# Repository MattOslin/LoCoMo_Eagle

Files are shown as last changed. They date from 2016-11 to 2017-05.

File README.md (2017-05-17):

# LoCoMo

Eagle files for LoCoMo boards.

Motherboard is the breakout for ESP-12, including wiperboard, espboard, and usb board. The individual boards are the cut up sections. Note that the motherboard file is for reference only, and the individual boards are the only working copy.

Slipring is the slip ring/potentiometer.

Zigzag is an excellent sheet used to define the start and end points of the traces for the encoder. Look at the zigzag script to see how to format the output of the excel sheet for use in eagle.

DXF files for stencils can be created using the cream-dxf ulp.

The zip files are OSHPARK cam files.

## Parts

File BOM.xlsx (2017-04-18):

Item | Module Quantity | Unit Price | Unit Price @10 | Total | Digikey # | URL | NOTES
4 Position Wiper | 1 | 1.26 | 1.145 | 1.145 | 70AAJ-4-M0-ND | https://www.digikey.com/product-detail/en/bourns-inc/70AAJ-4-M0/70AAJ-4-M0-ND/1232565
Op amp | 1 | 0.43 | 0.349 | 0.349 | AZV321KSTR-G1DICT-ND | http://www.digikey.com/scripts/DkSearch/dksus.dll?Detail&itemSeq=224809805&uq=636271628868311434
2 Position contact | 2 | 0.86 | 0.759 | 1.518 | 70AAJ-2-M0-ND | https://www.digikey.com/product-detail/en/bourns-inc/70AAJ-2-M0/70AAJ-2-M0-ND/1232563
Motor driver | 1 | 1.33 | 1.181 | 1.181 | TB6593FNGCT-ND | http://www.digikey.com/scripts/DkSearch/dksus.dll?Detail&itemSeq=224809802&uq=636271628868311434
Inductor | 1 | 0.21 | 0.192 | 0.192 | 490-10563-1-ND | http://www.digikey.com/scripts/DkSearch/dksus.dll?Detail&itemSeq=224809801&uq=636271628868311434
Vertical mini usb | 1 | 1.04 | 0.918 | 0.918 | H125262-ND | https://www.digikey.com/product-detail/en/hirose-electric-co-ltd/ZX80-B-5P(30)/H125262-ND/5994728
Regulator | 1 | 1.59 | 1.425 | 1.425 | 296-41856-1-ND | http://www.digikey.com/scripts/DkSearch/dksus.dll?Detail&itemSeq=224809799&uq=636271628868311434
Switch | 1 | 0.25 | 0.232 | 0.232 | RN1906FELF(CTCT-ND | http://www.digikey.com/scripts/DkSearch/dksus.dll?Detail&itemSeq=224809798&uq=636271628868311434
Power diode | 1 | 0.36 | 0.291 | 0.291 | B130-FDICT-ND | http://www.digikey.com/scripts/DkSearch/dksus.dll?Detail&itemSeq=224809794&uq=636271634297267434
Bi-LED | 1 | 0.44 | 0.311 | 0.311 | 160-2026-1-ND | http://www.digikey.com/product-detail/en/lite-on-inc/LTST-C235KGKRKT/160-2026-1-ND/3711391
CCR | 1 | 0.44 | 0.374 | 0.374 | NSI45020AT1GOSCT-ND | https://www.digikey.com/product-detail/en/on-semiconductor/NSI45020AT1G/NSI45020AT1GOSCT-ND/2096225
Button | 1 | 0.28 | 0.268 | 0.268 | CKN10502CT-ND | https://www.digikey.com/product-detail/en/c-k/PTS810-SJM-250-SMTR-LFS/CKN10502CT-ND/4176673
Clock | 1 | 1.11 | 0.984 | 0.984 | 631-1116-1-ND | http://www.digikey.com/scripts/DkSearch/dksus.dll?Detail&itemSeq=224809792&uq=636271634297267434
Header pins | 1 | 0.56 | 0.389 | 0.389 | S9014E-04-ND | https://www.digikey.com/product-detail/en/sullins-connector-solutions/GRPB041VWVN-RC/S9014E-04-ND/1786440
CH340G | 1 | 0.5 | 0.25 | 0.25 |  | EBAY
ESP12 | 1 | 2 | 1 | 1
1K Resistor | 2 |  |  |  |  |  | STOCK
5.1K Resistor | 1
330Ohm Resistor | 2
10K Resistor | 5 |  |  |  |  |  | STOCK
470Ohm Resistor | 2
100nF Capacitor | 5
10uF Capacitor | 3
2.2uF Capacitor | 1 |  |  |  |  |  | STOCK
22uF Capacitor | 1 |  |  |  |  |  | STOCK
10pF Capacitor | 1 |  |  |  |  |  | STOCK
15pF Capacitor | 1
 |  |  |  | 10.827

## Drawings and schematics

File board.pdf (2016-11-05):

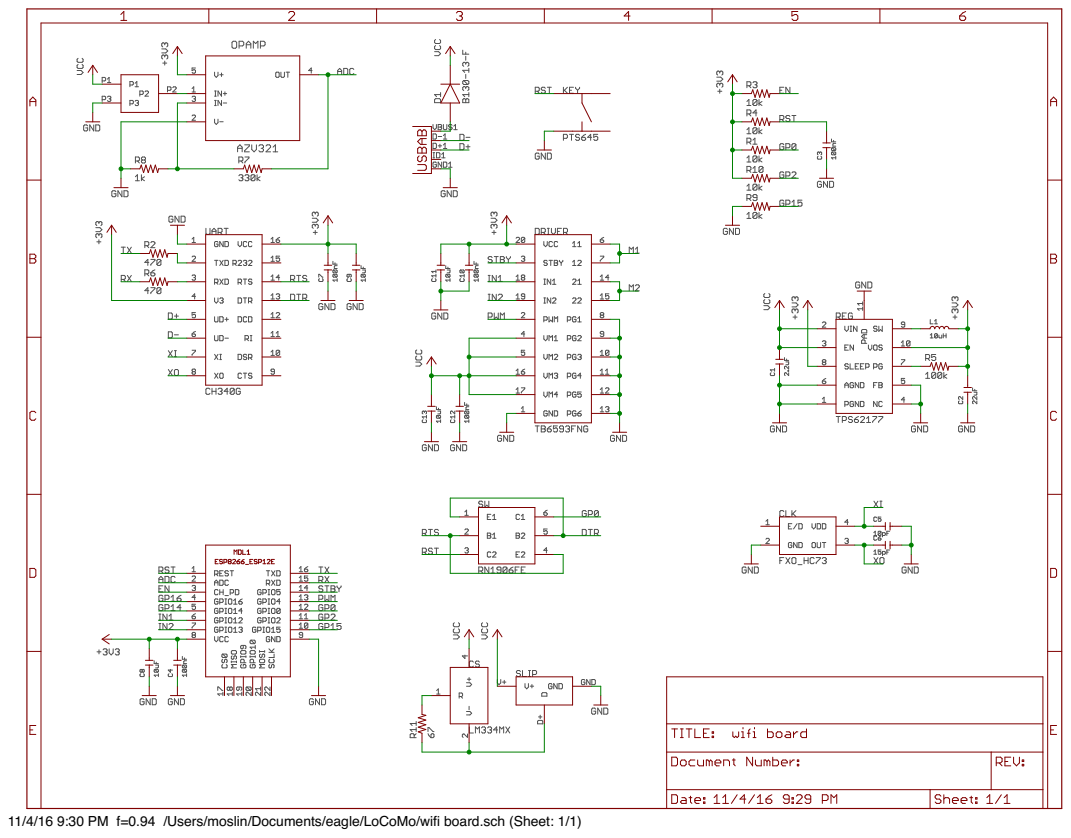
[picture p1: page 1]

11/4/16 9:30 PM f=0.94 /Users/moslin/Documents/eagle/LoCoMo/wifi board.sch (Sheet: 1/1)

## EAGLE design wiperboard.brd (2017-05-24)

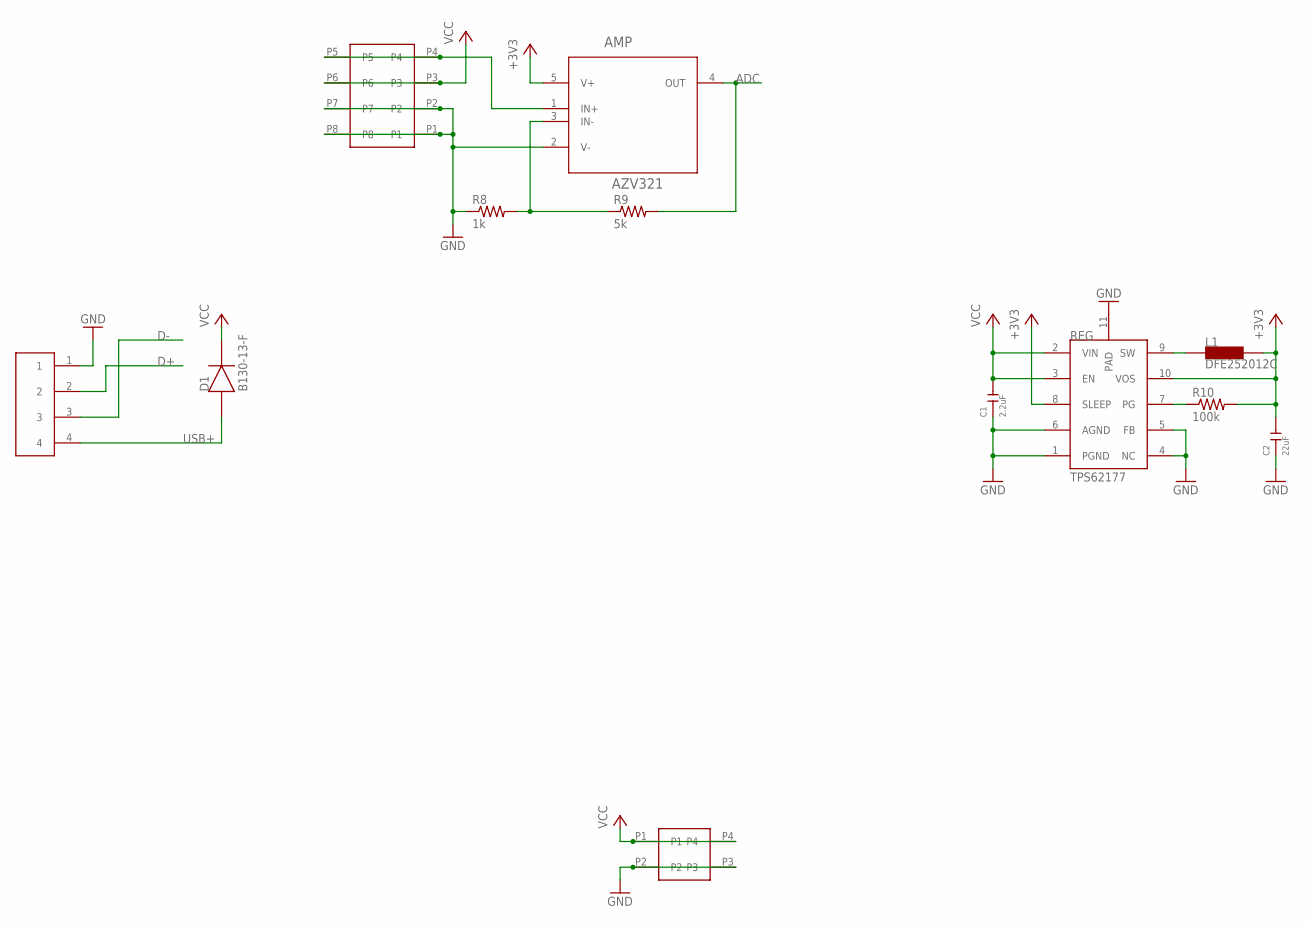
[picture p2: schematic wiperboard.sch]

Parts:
AMP: AZV321; SOT65P210X110-5N
C1: 2.2uF; C0603
C2: 22uF; C0603
CONN: BOURNS_2PIN
D1: B130-13-F; SMA
L1: DFE252012C; 1008
R8: 1k; R0603
R9: 5k; R0603
R10: 100k; R0603
REG: TPS62177; WSON-10
U$3: 4PIN_HEADER
WIPER: BOURNS_4PIN

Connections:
+3V3: AMP.5 (V+), C2.2, L1.P$3, R10.2, REG.8 (SLEEP), REG.10 (VOS)
ADC: AMP.4 (OUT), R9.2
D+: U$3.2
D-: U$3.3
GND: AMP.2 (V-), C1.1, C2.1, CONN.P2, CONN.P3, R8.1, REG.1 (PGND), REG.4 (NC), REG.5 (FB), REG.6 (AGND), REG.11 (PAD), U$3.1, WIPER.P1, WIPER.P2, WIPER.P7, WIPER.P8
unnamed: R10.1, REG.7 (PG)
unnamed: AMP.1 (IN+), WIPER.P4, WIPER.P5
unnamed: AMP.3 (IN-), R8.2, R9.1
SW: L1.P$2, REG.9 (SW)
USB+: D1.AN, U$3.4
VCC: C1.2, CONN.P1, CONN.P4, D1.CATH, REG.2 (VIN), REG.3 (EN), WIPER.P3, WIPER.P6

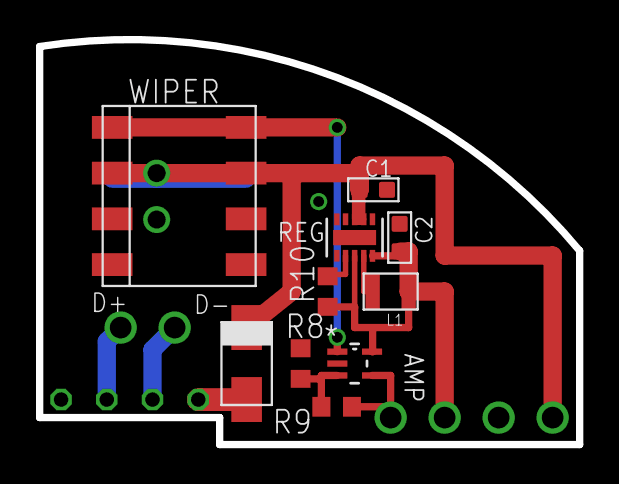
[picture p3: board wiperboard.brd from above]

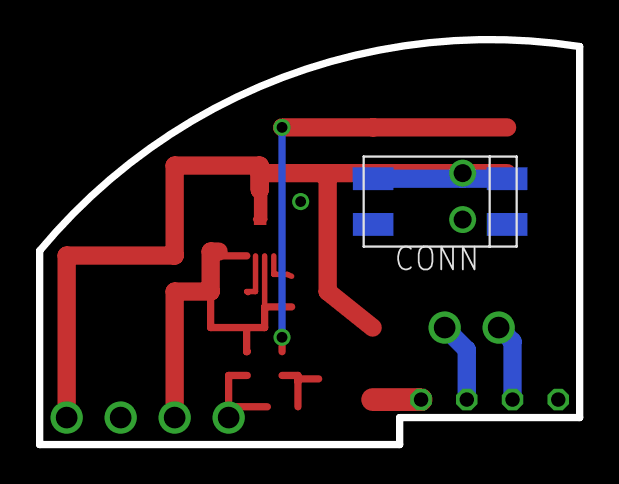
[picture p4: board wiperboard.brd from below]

Board: 2 copper layers, 30.0 x 22.5 mm, 12 parts (2 on the bottom side), 9 nets.

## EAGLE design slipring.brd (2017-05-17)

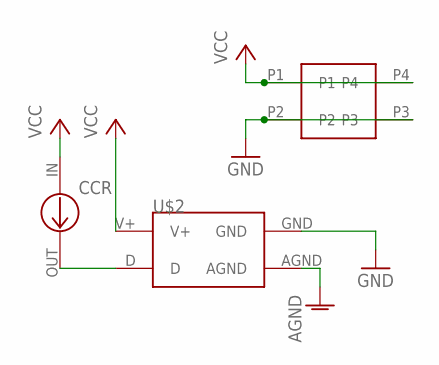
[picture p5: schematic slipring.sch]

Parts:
CCR: CCR
CONN: BOURNS_2PIN
U$2: RING3

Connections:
AGND: U$2.AGND
GND: CONN.P2, CONN.P3, U$2.GND
unnamed: CCR.OUT, U$2.D
VCC: CCR.IN, CONN.P1, CONN.P4, U$2.V+

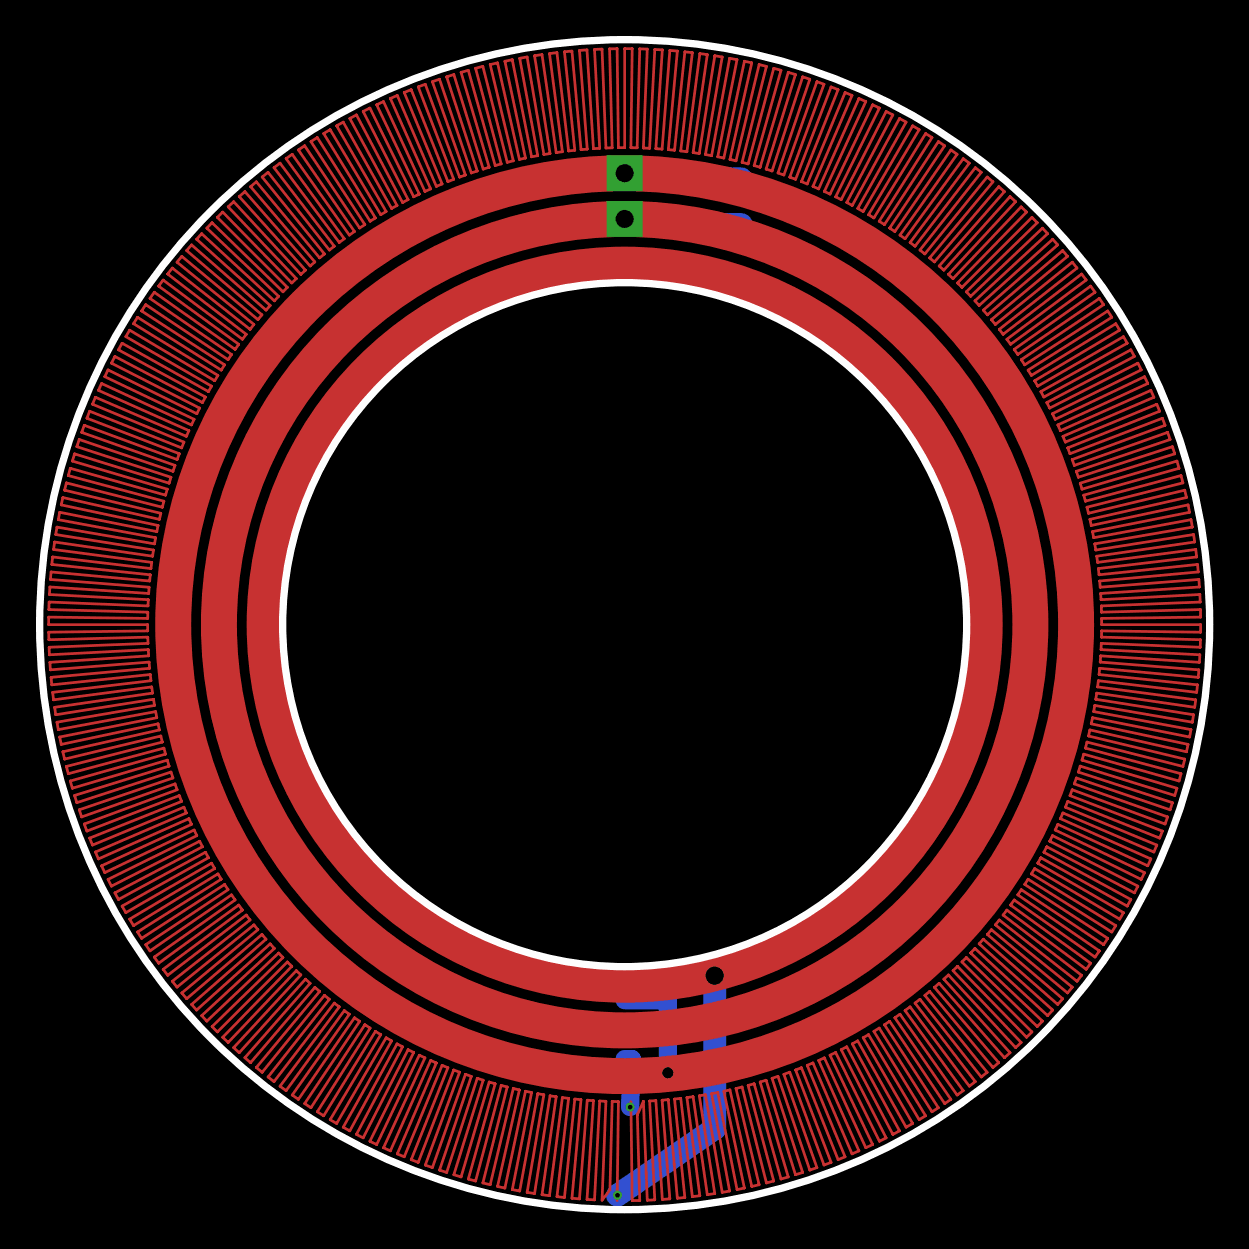
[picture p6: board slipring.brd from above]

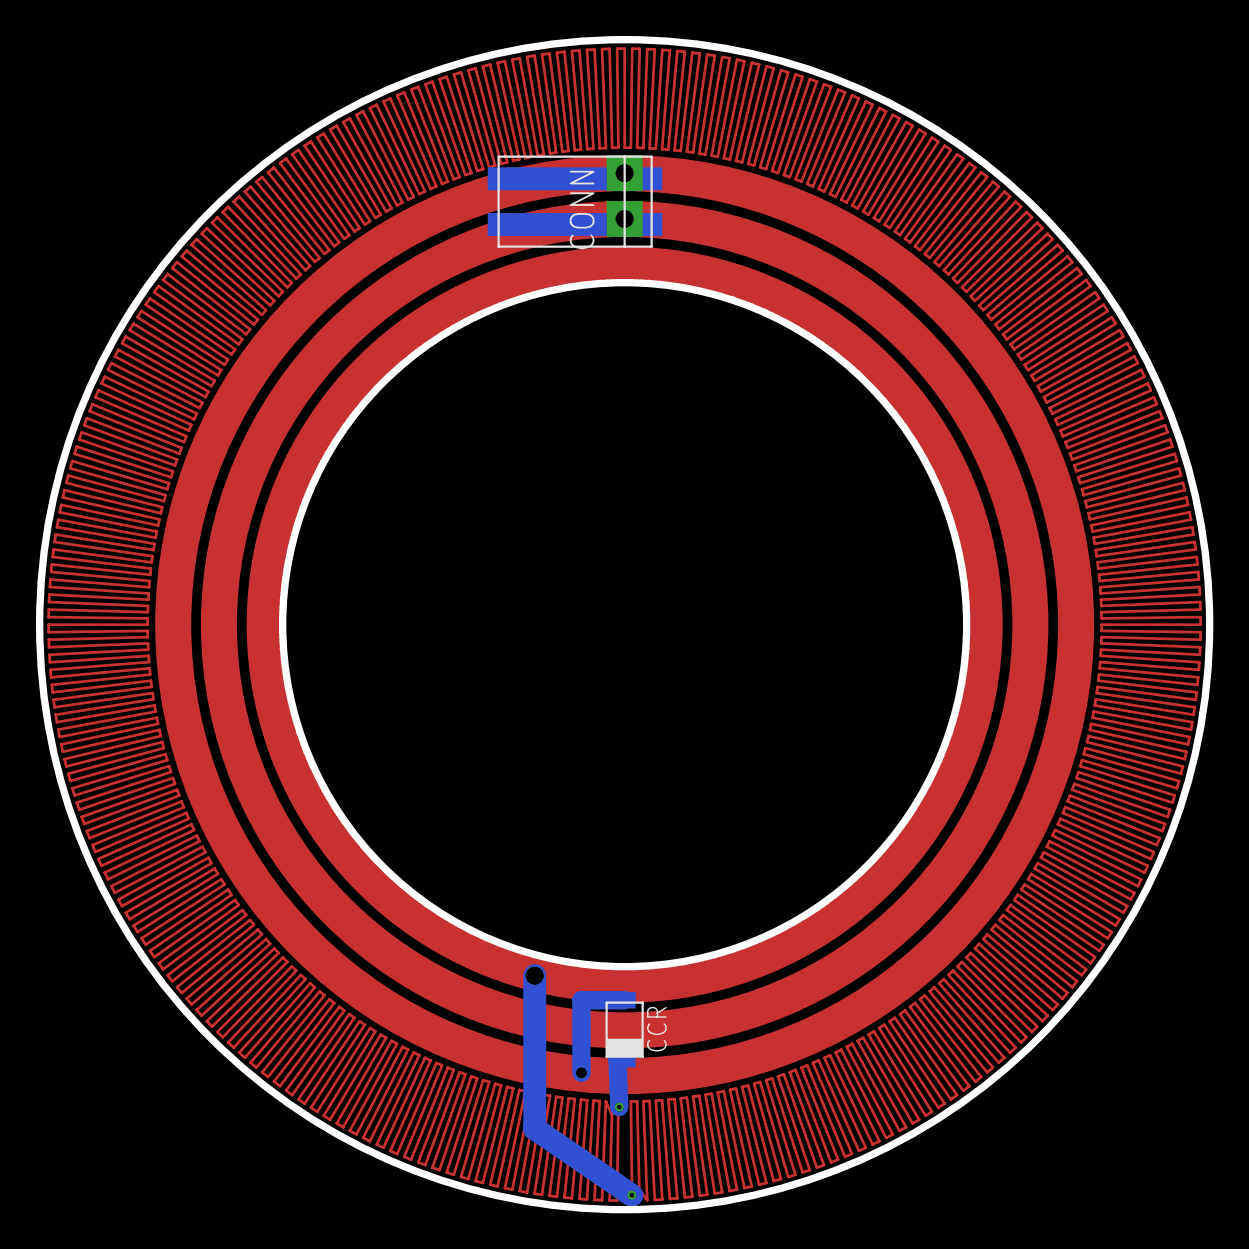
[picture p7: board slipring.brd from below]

Board: 2 copper layers, 65.0 x 65.0 mm, 3 parts (2 on the bottom side), 3 nets.

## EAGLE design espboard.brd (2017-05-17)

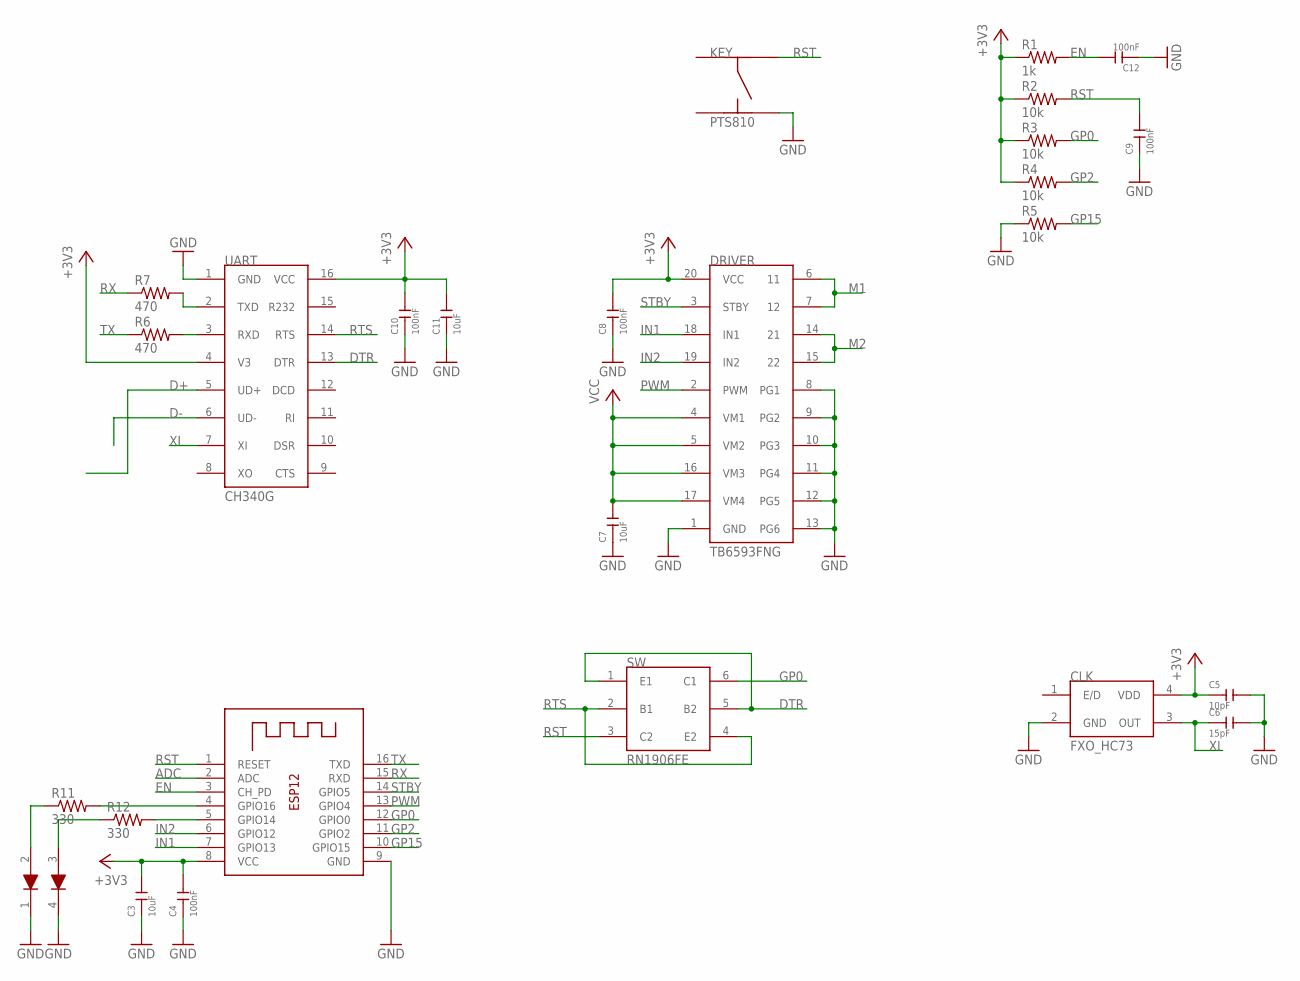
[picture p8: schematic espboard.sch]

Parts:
C3, C7, C11: 10uF; C0603
C4, C8, C9, C10, C12: 100nF; C0603
C5: 10pF; C0603
C6: 15pF; C0603
CLK: FXO_HC73; 4-SMD
DRIVER: TB6593FNG; SSOP-20
ESP12: ESP-12
KEY: PTS810; BUTTON
R1: 1k; R0603
R2, R3, R4, R5: 10k; R0603
R6, R7: 470; R0603
R11, R12: 330; R0603
SW: RN1906FE; SOT-563
U$2: BI_LED
UART: CH340G; 20-16

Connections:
+3V3: C3.2, C4.2, C5.1, C8.2, C10.2, C11.2, CLK.4 (VDD), DRIVER.20 (VCC), ESP12.8 (VCC), R1.1, R2.1, R3.1, R4.1, UART.4 (V3), UART.16 (VCC)
ADC: ESP12.2 (ADC)
D+: UART.5 (UD+)
D-: UART.6 (UD-)
DTR: SW.1 (E1), SW.5 (B2), UART.13 (DTR)
EN: C12.2, ESP12.3 (CH_PD), R1.2
GND: C3.1, C4.1, C5.2, C6.2, C7.1, C8.1, C9.1, C10.1, C11.1, C12.1, CLK.2 (GND), DRIVER.1 (GND), DRIVER.8 (PG1), DRIVER.9 (PG2), DRIVER.10 (PG3), DRIVER.11 (PG4), DRIVER.12 (PG5), DRIVER.13 (PG6), ESP12.9 (GND), KEY.4, R5.1, U$2.1, U$2.4, UART.1 (GND)
GP0: ESP12.12 (GPIO0), R3.2, SW.6 (C1)
GP2: ESP12.11 (GPIO2), R4.2
GP15: ESP12.10 (GPIO15), R5.2
IN1: DRIVER.18 (IN1), ESP12.7 (GPIO13)
IN2: DRIVER.19 (IN2), ESP12.6 (GPIO12)
M1: DRIVER.6 (11), DRIVER.7 (12)
M2: DRIVER.14 (21), DRIVER.15 (22)
unnamed: R7.2, UART.2 (TXD)
unnamed: R6.2, UART.3 (RXD)
unnamed: ESP12.5 (GPIO14), R12.2
unnamed: ESP12.4 (GPIO16), R11.2
unnamed: R11.1, U$2.2
unnamed: R12.1, U$2.3
PWM: DRIVER.2 (PWM), ESP12.13 (GPIO4)
RST: C9.2, ESP12.1 (RESET), KEY.2, R2.2, SW.3 (C2)
RTS: SW.2 (B1), SW.4 (E2), UART.14 (RTS)
RX: ESP12.15 (RXD), R7.1
STBY: DRIVER.3 (STBY), ESP12.14 (GPIO5)
TX: ESP12.16 (TXD), R6.1
VCC: C7.2, DRIVER.4 (VM1), DRIVER.5 (VM2), DRIVER.16 (VM3), DRIVER.17 (VM4)
XI: C6.1, CLK.3 (OUT), UART.7 (XI)

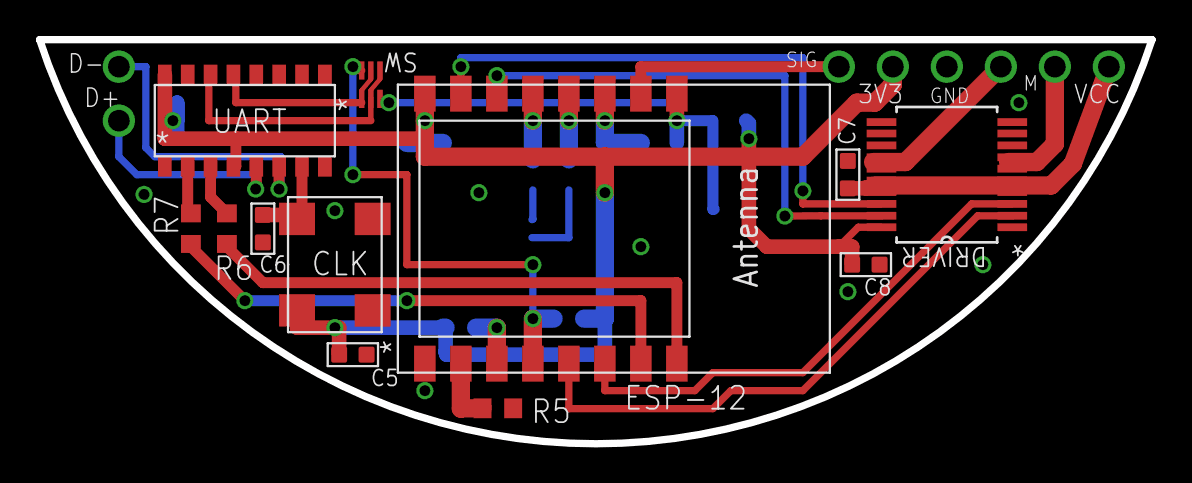
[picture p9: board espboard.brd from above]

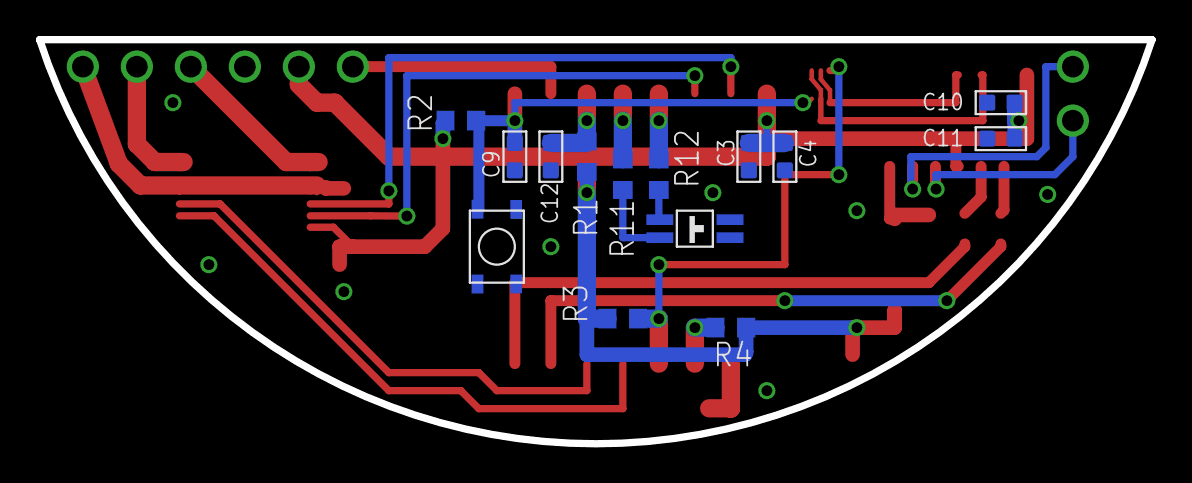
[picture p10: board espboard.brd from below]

Board: 2 copper layers, 61.8 x 22.5 mm, 26 parts (14 on the bottom side), 25 nets.

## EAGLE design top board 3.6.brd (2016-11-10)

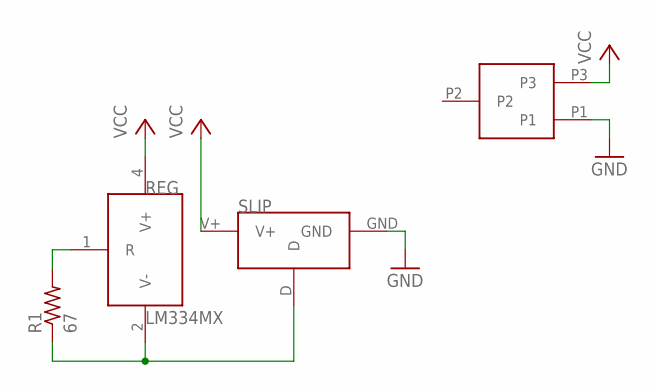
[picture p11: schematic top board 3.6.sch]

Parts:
R1: 67; R0603
REG: LM334MX; 8-SOIC
SLIP: RING2
U$2: AVX_CONN

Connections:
GND: SLIP.GND, U$2.P1
unnamed: R1.2, REG.1 (R)
unnamed: R1.1, REG.2 (V-), SLIP.D
VCC: REG.4 (V+), SLIP.V+, U$2.P3

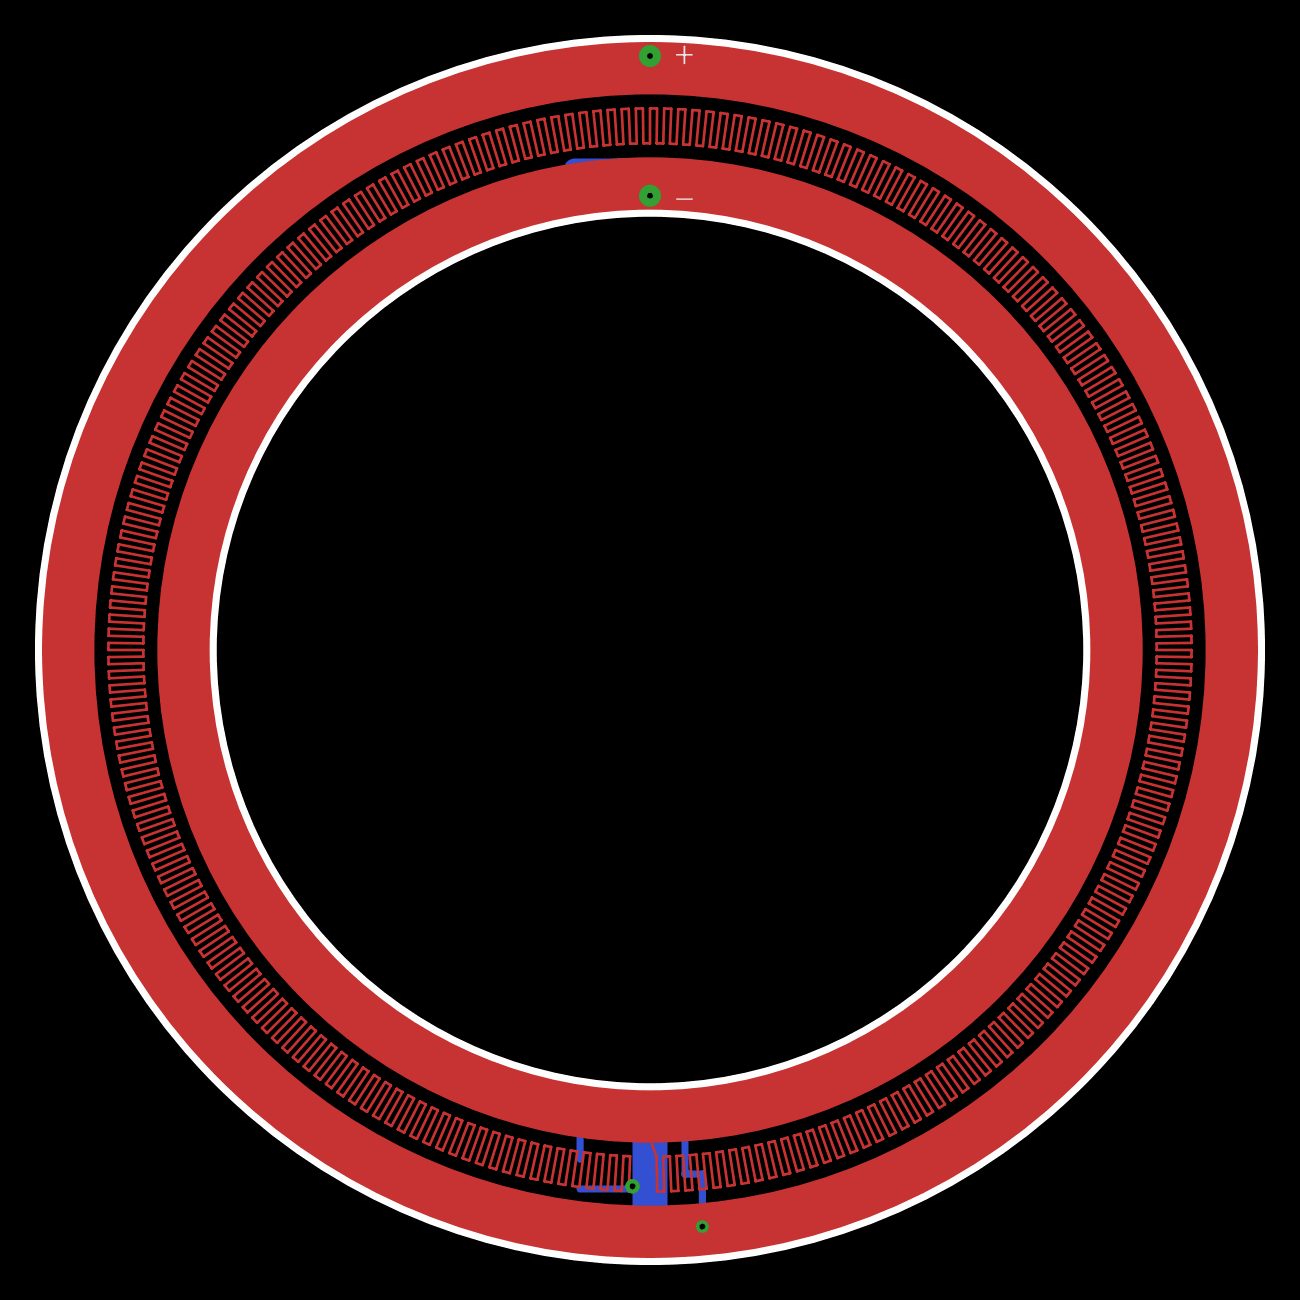
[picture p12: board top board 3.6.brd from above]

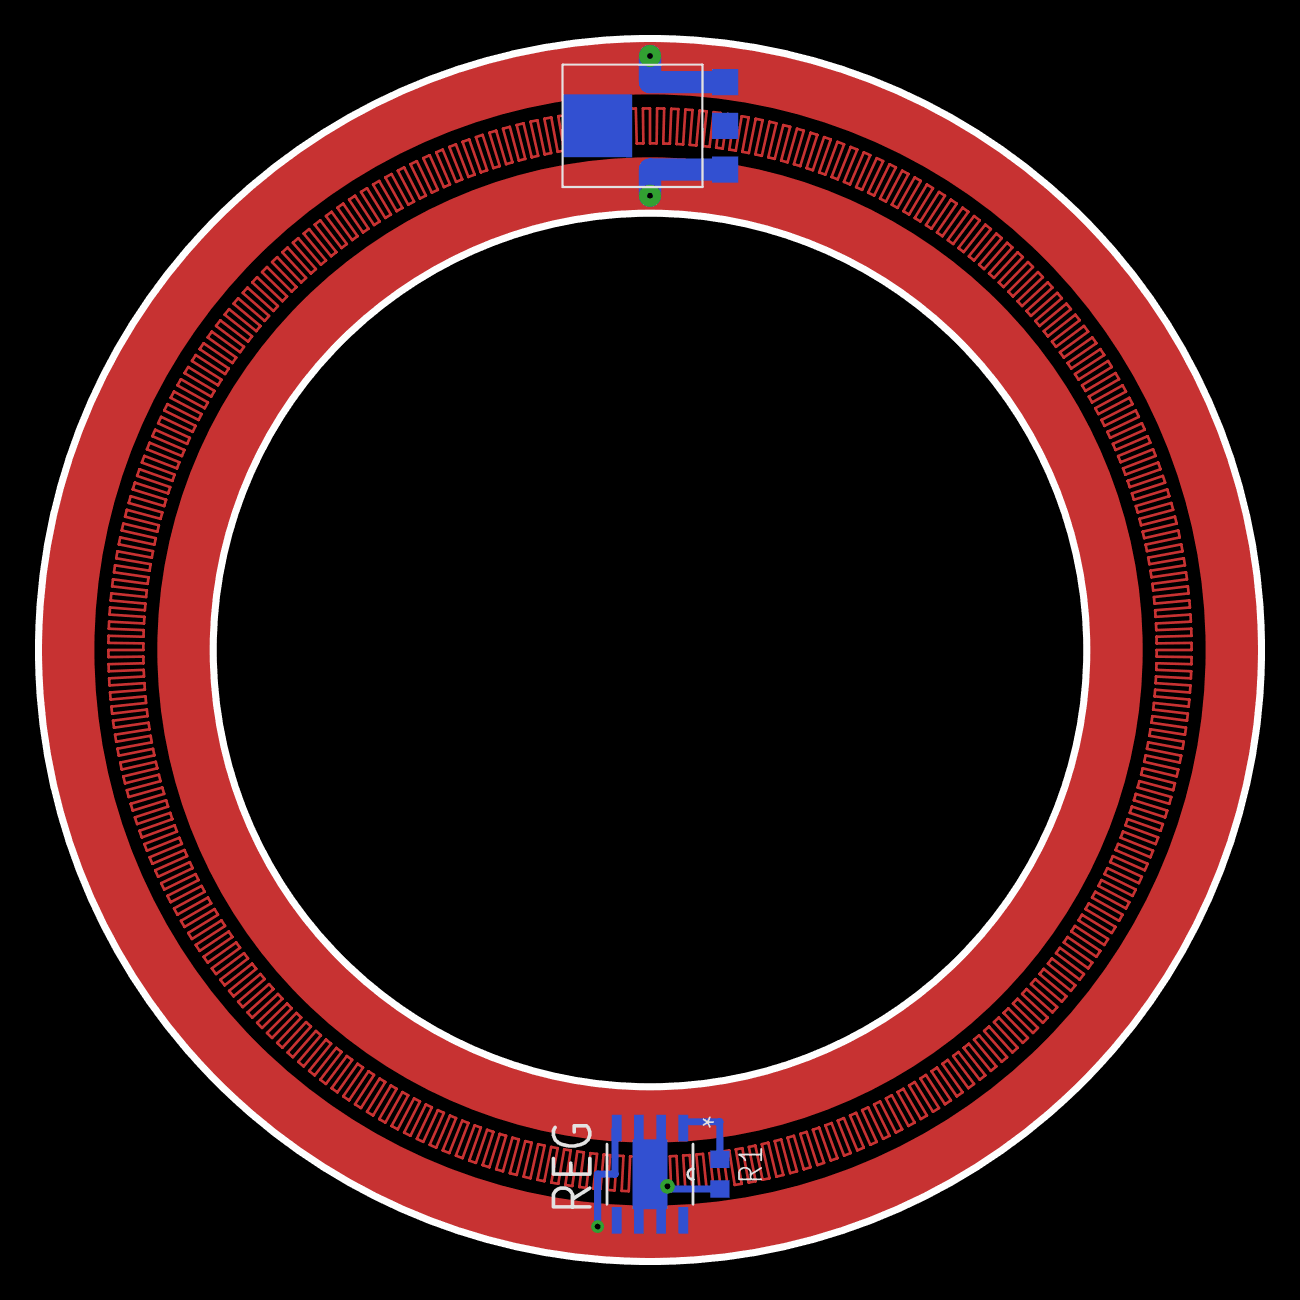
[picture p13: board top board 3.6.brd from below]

Board: 2 copper layers, 70.0 x 70.0 mm, 4 parts (3 on the bottom side), 4 nets.

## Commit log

2016-11-05 pdf schematic
2016-11-10 began routing
    [top board 3.6.brd, top board 3.6.sch, top board.brd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]
2016-11-12 finished routing and made gerber files
    [wifi board.brd, wifi board.sch]
2016-11-14 added logo, optimized ground pours
    [wifi board.brd, wifi board.sch]
2016-12-18 fixed motherboard after initial tests
    [motherboard.brd, motherboard.sch]
2017-03-28 Add files via upload
    Final version of gen1 boards, added initial cad of slipring with analog ground, switching to bourns connectors
    [motherboard.brd, slipring.brd, slipring.sch]
2017-03-28 started work on revised board
    [motherboard.brd, motherboard.sch, top board 3.6.brd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]
2017-03-28 switched to 20mA reg
    [slipring.brd, slipring.sch]
2017-04-01 more routing
    [motherboard.brd, motherboard.sch]
2017-04-03 final routing before splitting up boards
    [motherboard.brd, motherboard.sch]
2017-04-03 split board into three parts, cam processed
    [espboard.brd, espboard.sch, usbboard.brd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]
2017-04-04 final cad for purchase
    [espboard.brd, slipring.brd, slipring.sch]
2017-04-18 Added BOM, updated resistor values
    [BOM.xlsx, motherboard.brd, motherboard.sch]
2017-04-18 updated bom
    [BOM.xlsx]
2017-05-17 fixed intial board errors, including short, flipped usb, and missing trace
    [espboard.brd, espboard.sch, slipring.brd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]
2017-05-24 fixed collision issue
    [usbboard.brd, wiperboard.brd]
